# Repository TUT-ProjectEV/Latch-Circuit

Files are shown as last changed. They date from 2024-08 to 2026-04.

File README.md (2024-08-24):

# Latch-Circuit

## Version
- v1.1

## Overview
- AMS, BSPD, IMDからの信号をモニタ・ラッチしてSDN回路に接続されるリレーをドライブする回路
- AMS, BSPD, IMDのインジケータドライブ回路

## Requirement
### Development
- Kicad 7.0
### Libraries
- ProjectEV-Kicad-Library
    - v7.0

## Usage
- Vsupply: 12V
- AMS, BSPD, IMD Signal Input Level: L=0V, H=12V

## Features
- MOSFETによるラッチング、リレードライブ
- AMS, BSPD, IMD信号入力はMOSFETのゲートであるため、ロジックレベルは3.3V~12Vまで対応可能

## Reference
- ["Reference Site Name"]("Reference URL")

## Author
- [ST04-tkmr](https://github.com/ST04-tkmr)

## License
- Copyright (c) 2024 東京工科大学 ProjectEV

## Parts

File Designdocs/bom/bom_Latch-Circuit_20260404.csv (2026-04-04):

Reference | Value | Footprint | Qty | DNP | Mouser番号 | digikey品番
C1 | 22u | ProjectEV_Capacitor:C_3216M | 1
C2,C4,C5,C6 | 10n | ProjectEV_Capacitor:C_1608M | 4
C3 | 100n | ProjectEV_Capacitor:C_1608M | 1
C7 | 1n | ProjectEV_Capacitor:C_3216M | 1
D1 | PZ1AH11B-AU_R1_000A1 | ProjectEV_Diode:PZ1AH11B-AU_R1_000A1 | 1 |  | 241-PZ1AH11BAUR1000A
D2,D4,D5,D6 | B1911PG--20D000514U1930 | ProjectEV_LED:B1911PG--20D000514U1930 | 4 |  |  | 3147-B1911PG--20D000514U1930CT-ND
D3 | CUHZ20V,H3F | ProjectEV_Protection:CUHZ20V,H3F | 1 |  |  | 264-CUHZ20VH3FCT-ND
D7,D8,D9 | B1911USD-20D000114U1930 | ProjectEV_LED:B1911USD-20D000114U1930 | 3 |  |  | 3147-B1911USD-20D000114U1930CT-ND
F1 | 0ABB-1000-TM | ProjectEV_Fuse:0ABB-1000-TM | 1 |  | 530-0ABB-1000-TM | 507-0ABB-5000-TMCT-ND
J1 | 2-1445052-2 | ProjectEV_Connector:2-1445052-2 | 1 |  | 571-2-1445052-2
J2 | 3-794633-8 | ProjectEV_Connector:3-794633-8 | 1 |  | 571-3-794633-8
J3 | B2P-VH | ProjectEV_Connector_JST:B2P-VH | 1 |  |  | 455-1639-ND
J4 | 3-794633-6 | ProjectEV_Connector:3-794633-6 | 1 |  | 571-3-794633-6
Q1 | DMP3098LQ-7 | ProjectEV_Transistor:DMP3098LQ-7 | 1 |  | 621-DMP3098LQ-7
Q2,Q3,Q4 | 2N7002K-AU_R1_000A2 | ProjectEV_Transistor:2N7002K-AU_R1_000A2 | 3 |  |  | 3757-2N7002K-AU_R1_000A2CT-ND
R1,R2,R8,R9,R12,R15,R28,R29,R30,R31,R32,R33 | 10k | ProjectEV_Resistor:R_1608M | 12
R3,R4,R5,R6 | 0 | ProjectEV_Resistor:R_1608M | 4
R7,R10,R13,R16,R19,R22,R25 | 100 | ProjectEV_Resistor:R_1608M | 7
R11,R14,R17,R20,R23,R26 | 100k | ProjectEV_Resistor:R_1608M | 6
R18,R21,R24 | 1.2k | ProjectEV_Resistor:R_3216M | 3
R27 | 1M | ProjectEV_Resistor:R_3216M | 1
U1,U2,U3 | TLP3106A(TP,F | ProjectEV_Relay:TLP3106A(TP,F | 3 |  | 757-TLP3106A(TP,F
U4 | CD4043BPWR | ProjectEV_Logic:CD4043BPWR | 1 |  | 595-CD4043BPWR
U5 | TBD62003AFNG,EL | ProjectEV_PowerManagement:TBD62003AFNG,EL | 1 |  | 757-TBD62003AFNGEL

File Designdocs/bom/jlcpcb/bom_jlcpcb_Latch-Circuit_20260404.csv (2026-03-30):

Comment | Designator | Footprint | LCSC | Quantity
0 | R3,R4,R5,R6 | R_1608M | C21189 | 4
1.2k | R18,R21,R24 | R_3216M | C22765 | 3
100 | R10,R13,R16,R19,R22,R25,R7 | R_1608M | C22775 | 7
100k | R11,R14,R17,R20,R23,R26 | R_1608M | C25803 | 6
100n | C3 | C_1608M | C14663 | 1
10k | R1,R12,R15,R2,R28,R29,R30,R31,R32,R33,R8,R9 | R_1608M | C25804 | 12
10n | C2,C4,C5,C6 | C_1608M | C57112 | 4
22u | C1 | C_3216M | C12891 | 1
MouseBites_5.0mm_OneSide | REF** | MouseBites_5.0mm_OneSide |  | 1

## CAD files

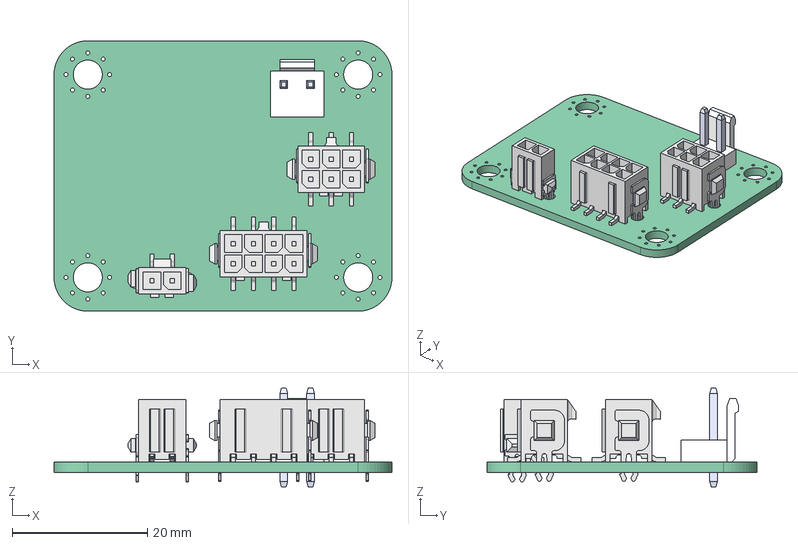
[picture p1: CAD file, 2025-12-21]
Designdocs/3dmodel/Latch-Circuit_20251221.step
50.0 x 40.0 x 14.6 mm

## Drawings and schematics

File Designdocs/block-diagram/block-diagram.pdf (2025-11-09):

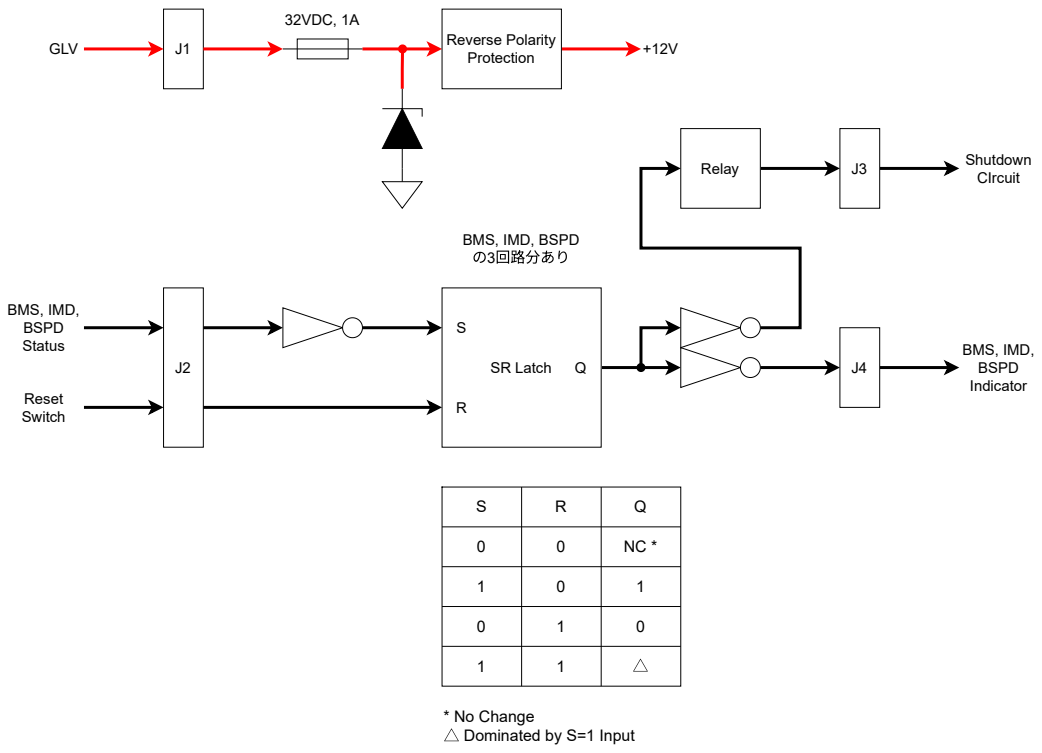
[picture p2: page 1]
32VDC, 1A; Reverse Polarity Protection; GLV; BMS, IMD, BSPD Status; Reset Switch; SR Latch; Relay; Shutdown; CIrcuit; BMS, IMD, BSPD Indicator

BMS, IMD, BSPD
の3回路分あり

* No Change
△ Dominated by S=1 Input

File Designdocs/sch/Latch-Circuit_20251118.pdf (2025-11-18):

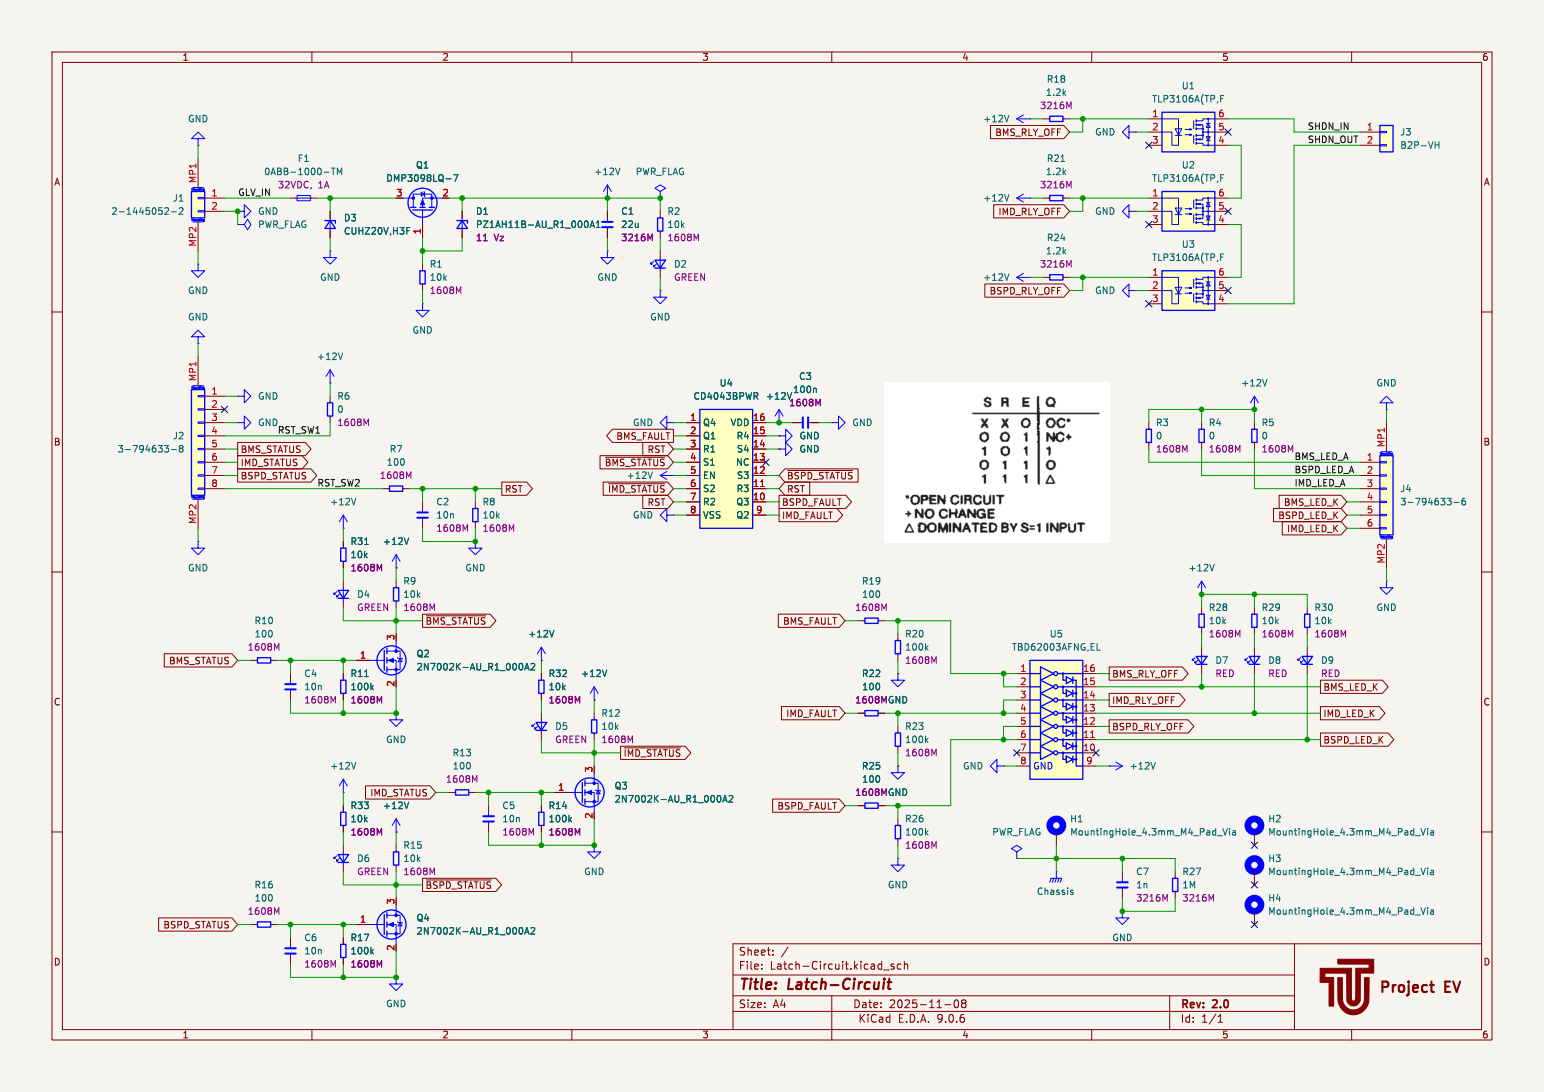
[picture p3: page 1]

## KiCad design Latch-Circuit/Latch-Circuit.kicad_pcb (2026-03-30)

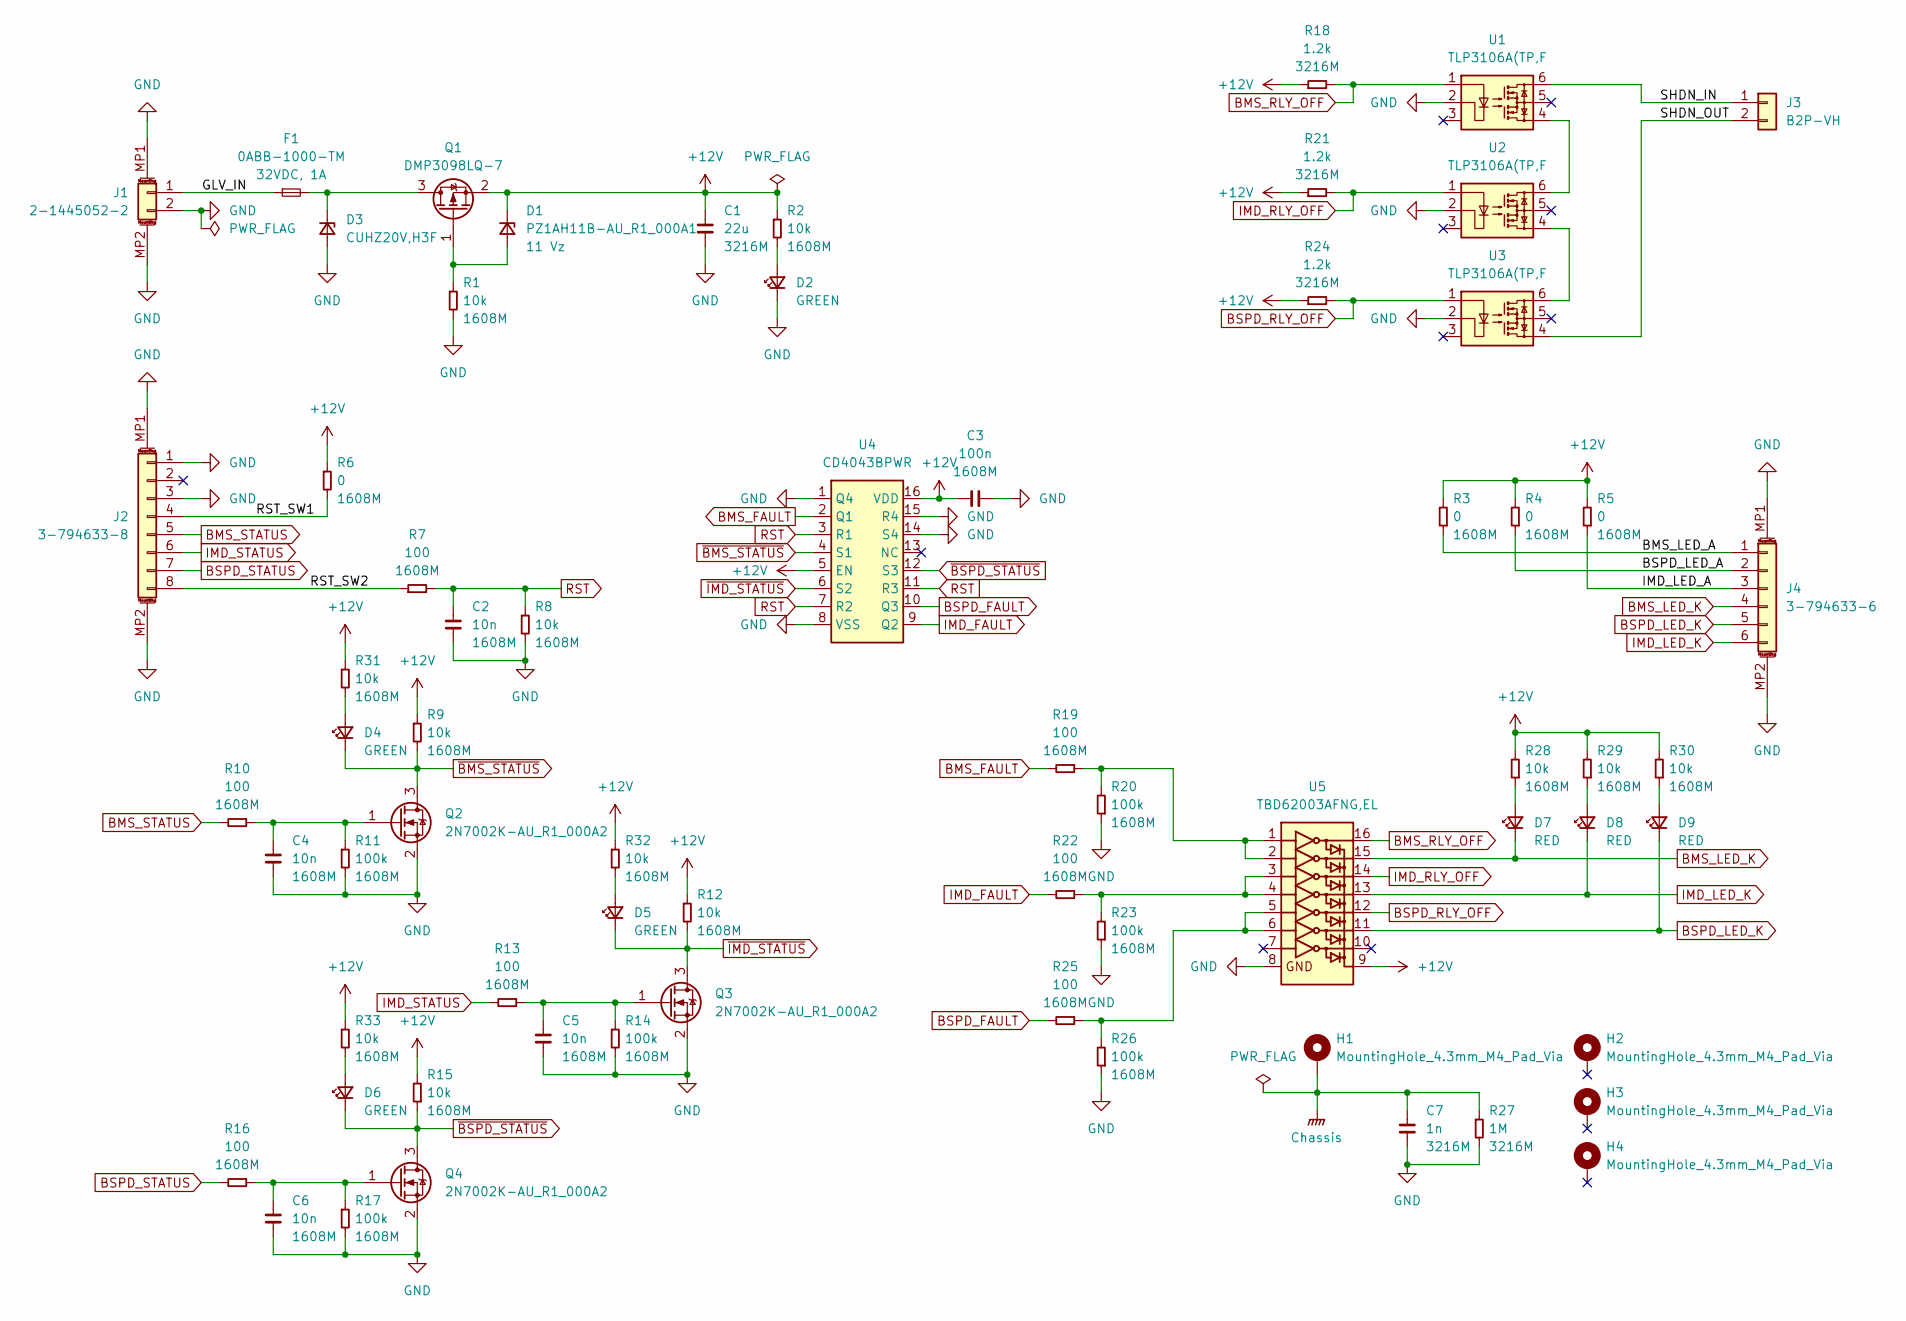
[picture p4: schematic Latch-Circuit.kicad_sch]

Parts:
C1: 22u; C_3216M
C2, C4, C5, C6: 10n; C_1608M
C3: 100n; C_1608M
C7: 1n; C_3216M
D1: PZ1AH11B-AU_R1_000A1; Mouser番号 241-PZ1AH11BAUR1000A
D2, D4, D5, D6: B1911PG--20D000514U1930; digikey品番 3147-B1911PG--20D000514U1930CT-ND
D3: CUHZ20V,H3F; digikey品番 264-CUHZ20VH3FCT-ND
D7, D8, D9: B1911USD-20D000114U1930; digikey品番 3147-B1911USD-20D000114U1930CT-ND
F1: 0ABB-1000-TM; digikey品番 507-0ABB-5000-TMCT-ND
H1, H2, H3, H4: MountingHole_4.3mm_M4_Pad_Via
J1: 2-1445052-2; Mouser番号 571-2-1445052-2
J2: 3-794633-8; Mouser番号 571-3-794633-8
J3: B2P-VH; digikey品番 455-1639-ND
J4: 3-794633-6; Mouser番号 571-3-794633-6
Q1: DMP3098LQ-7; Mouser番号 621-DMP3098LQ-7
Q2, Q3, Q4: 2N7002K-AU_R1_000A2; digikey品番 3757-2N7002K-AU_R1_000A2CT-ND
R1, R2, R8, R9, R12, R15, R28, R29, R30, R31, R32, R33: 10k; R_1608M
R3, R4, R5, R6: 0; R_1608M
R7, R10, R13, R16, R19, R22, R25: 100; R_1608M
R11, R14, R17, R20, R23, R26: 100k; R_1608M
R18, R21, R24: 1.2k; R_3216M
R27: 1M; R_3216M
U1, U2, U3: TLP3106A(TP,F; Mouser番号 757-TLP3106A(TP,F
U4: CD4043BPWR; Mouser番号 595-CD4043BPWR
U5: TBD62003AFNG,EL; Mouser番号 757-TBD62003AFNGEL

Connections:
+12V: C1.1, C3.1, D1.1 (K), Q1.2 (S), R2.1, R3.2, R4.2, R5.2, R6.1, R9.1, R12.1, R15.2, R18.1, R21.1, R24.1, R28.2, R29.2, R30.2, R31.1, R32.1, R33.1, U4.5 (EN), U4.16 (VDD), U5.9 (COMMON)
/BMS_LED_A: J4.1, R3.1
/BSPD_LED_A: J4.2, R4.1
/GLV_IN: F1.1, J1.1
/IMD_LED_A: J4.3, R5.1
/RST_SW1: J2.4, R6.2
/RST_SW2: J2.8, R7.1
/SHDN_IN: J3.1, U1.6 (Drain)
/SHDN_OUT: J3.2, U3.4 (Drain)
BMS_FAULT: R19.2, U4.2 (Q1)
BMS_LED_K: D7.1 (K), J4.4, U5.15 (O2)
BMS_RLY_OFF: R18.2, U1.1 (Anode), U5.16 (O1)
BMS_STATUS: J2.5, R10.2
BSPD_FAULT: R25.2, U4.10 (Q3)
BSPD_LED_K: D9.1 (K), J4.5, U5.11 (O6)
BSPD_RLY_OFF: R24.2, U3.1 (Anode), U5.12 (O5)
BSPD_STATUS: J2.7, R16.2
Chassis: C7.1, H1.MP, R27.1
GND: C1.2, C2.2, C3.2, C4.2, C5.2, C6.2, C7.2, D2.1 (K), D3.2 (A), J1.2, J1.MP1 (MountPin), J1.MP2 (MountPin), J2.1, J2.3, J2.MP1 (MountPin), J2.MP2 (MountPin), J4.MP1 (MountPin), J4.MP2 (MountPin), Q2.2 (S), Q3.2 (S), Q4.2 (S), R1.2, R8.2, R11.2, R14.2, R17.2, R20.1, R23.1, R26.1, R27.2, U1.2 (Cathode), U2.2 (Cathode), U3.2 (Cathode), U4.1 (Q4), U4.8 (VSS), U4.14 (S4), U4.15 (R4), U5.8 (GND)
IMD_FAULT: R22.2, U4.9 (Q2)
IMD_LED_K: D8.1 (K), J4.6, U5.13 (O4)
IMD_RLY_OFF: R21.2, U2.1 (Anode), U5.14 (O3)
IMD_STATUS: J2.6, R13.2
unnamed: D1.2 (A), Q1.1 (G), R1.1
unnamed: D2.2 (A), R2.2
unnamed: D3.1 (K), F1.2, Q1.3 (D)
unnamed: D4.2 (A), R31.2
unnamed: D5.2 (A), R32.2
unnamed: D6.2 (A), R33.2
unnamed: D7.2 (A), R28.1
unnamed: D8.2 (A), R29.1
unnamed: D9.2 (A), R30.1
unnamed: C4.1, Q2.1 (G), R10.1, R11.1
unnamed: C5.1, Q3.1 (G), R13.1, R14.1
unnamed: C6.1, Q4.1 (G), R16.1, R17.1
unnamed: U1.4 (Drain), U2.6 (Drain)
unnamed: U2.4 (Drain), U3.6 (Drain)
unnamed: R19.1, R20.2, U5.1 (I1), U5.2 (I2)
unnamed: R22.1, R23.2, U5.3 (I3), U5.4 (I4)
unnamed: R25.1, R26.2, U5.5 (I5), U5.6 (I6)
RST: C2.1, R7.2, R8.1, U4.3 (R1), U4.7 (R2), U4.11 (R3)
~BMS_STATUS: D4.1 (K), Q2.3 (D), R9.2, U4.4 (S1)
~BSPD_STATUS: D6.1 (K), Q4.3 (D), R15.1, U4.12 (S3)
~IMD_STATUS: D5.1 (K), Q3.3 (D), R12.2, U4.6 (S2)

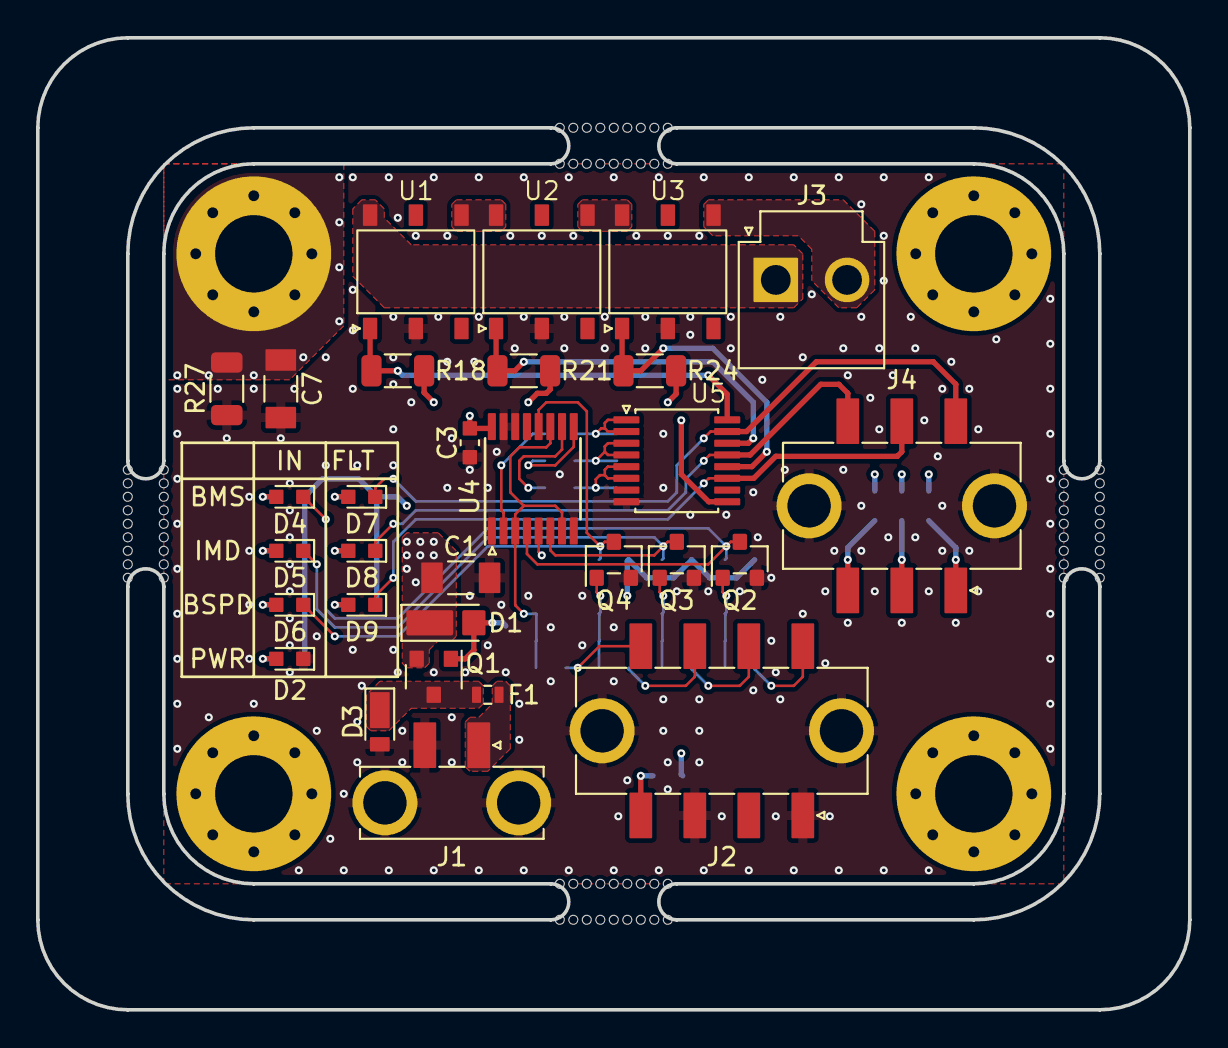
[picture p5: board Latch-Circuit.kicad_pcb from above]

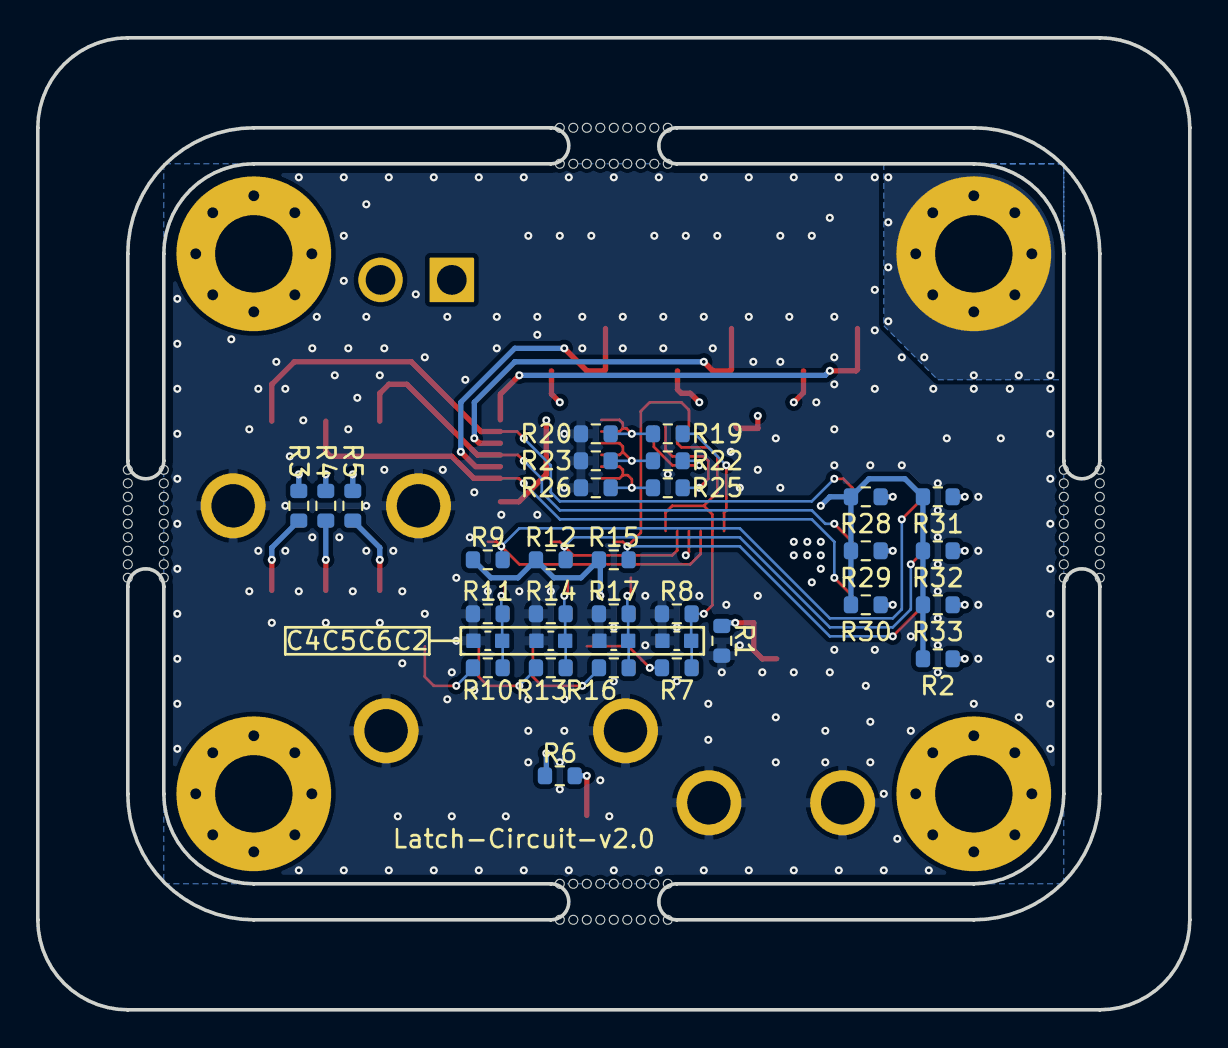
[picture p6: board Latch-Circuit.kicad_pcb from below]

Board: 4 copper layers, 64.0 x 54.0 mm, 67 parts (33 on the bottom side), 44 nets.

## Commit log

2024-03-17 create project
    [Latch-Circuit.kicad_pcb, Latch-Circuit.kicad_sch]
2024-03-17 add ignore folder
    Latch-Circuit-backups
2024-04-20 add sim file
    シミュレーション済み
2024-04-20 回路図完成、PCBCADに部品追加
    [Latch-Circuit.kicad_pcb, Latch-Circuit.kicad_sch]
2024-04-22 ラベル追加
    [Latch-Circuit.kicad_sch]
2024-04-22 若干配置
    [Latch-Circuit.kicad_pcb]
2024-04-24 コネクタをトップ型に変更、アノテーション、素子配置
    [Latch-Circuit.kicad_pcb, Latch-Circuit.kicad_sch]
2024-04-24 配線完了、リレー配線修正、外周ビア打ち
    [Latch-Circuit.kicad_pcb, Latch-Circuit.kicad_sch]
2024-04-25 完成
    最終チェック後、ガーバー出力
    [Latch-Circuit.kicad_pcb]
2024-04-25 原点位置の修正
    [Latch-Circuit.kicad_pcb]
2024-04-26 シャットダウンチェック用のTP追加
    [Latch-Circuit.kicad_pcb, Latch-Circuit.kicad_sch]
2024-04-28 1ピン識別子追加
    [Latch-Circuit.kicad_pcb]
2024-04-29 コメント追加
    [Latch-Circuit.kicad_sch]
2024-05-03 ベタ修正
    [Latch-Circuit.kicad_pcb]
2024-05-03 ガーバー、BOM出力
    [bom.csv, designators.csv, positions.csv]
2024-05-20 digikey用bom作成
    購入数未入力、他基板素子と同時発注のため
    [bom.xlsx, digikey-list.xlsx]
2024-05-20 ファイル名変更
    [bom_Latch-Circuit.xlsx, digikey-list_Latch-Circuit.xlsx]
2024-05-23 素子の説明追加
    [digikey-list_Latch-Circuit.xlsx]
2024-05-23 購入個数追加、csv出力
    [digikey-list_Latch-Circuit.csv, digikey-list_Latch-Circuit.xlsx]
2024-07-29 modify constant, add NOT for status LED
2024-07-29 modify constant, add circuits Rgs 1M->100k, NOT Circuit for status LED, LED for test
    [Latch-Circuit.kicad_sch]
2024-07-29 配置、配線終了
    [Latch-Circuit.kicad_pcb]
2024-07-30 complete AW, DRC next->select parts at JLCPCB
    [Latch-Circuit.kicad_pcb]
2024-07-30 PCBA用素子選定
2024-07-30 export step
    [Latch-Circuit.step]
2024-07-30 add 捨て基板, Toolinghole, Fiducial
    [Latch-Circuit.kicad_pcb]
2024-07-30 generate gerber, production file by JLCPCB Tools
    [BOM-Latch-Circuit.csv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]
2024-07-30 原点修正
    [Latch-Circuit.kicad_pcb]
2024-07-30 generate gerber and production files again
    [CPL-Latch-Circuit.csv, Latch-Circuit-CuBottom.gbr, Latch-Circuit-CuTop.gbr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]
2024-08-05 add JLCPCB PCBA BOM
    [bom.xls]
2024-08-23 README.md を更新
2025-11-08 create a new kicad project
    [Latch-Circuit.kicad_pcb, Latch-Circuit.kicad_sch]
2025-11-08 add title, revision, and date
    [Latch-Circuit.kicad_sch]
2025-11-08 add signal labels and power circuit
    [Latch-Circuit.kicad_sch]
2025-11-08 complete circuit design, not decide constraints
    [Latch-Circuit.kicad_sch]
2025-11-09 modify pin assigns, decide consts, and apply some changes
    [Latch-Circuit.kicad_sch]
2025-11-09 ERC done, and modify
    [Latch-Circuit.kicad_sch]
2025-11-09 create a new drawio project and add power circuit
2025-11-09 add footprints from sch
    [Latch-Circuit.kicad_pcb]
2025-11-09 add LEDs
    [Latch-Circuit.kicad_sch]
2025-11-09 change relay and led drive circuit
    [Latch-Circuit.kicad_sch]
2025-11-09 update relay and led drive circuit
2025-11-09 update footprints, and place components
    [Latch-Circuit.kicad_pcb]
2025-11-09 finish wiring
    [Latch-Circuit.kicad_pcb]
2025-11-15 add vias
    [Latch-Circuit.kicad_pcb]
2025-11-18 generate pdf of sch
    [Latch-Circuit.kicad_sch]
2025-11-18 add dimension line and DRC OK
    [Latch-Circuit.kicad_pcb]
2025-11-18 add jlcpcb tools database
    [Latch-Circuit.kicad_pcb]
2025-12-21 add pcb name
    [Latch-Circuit.kicad_pcb]
2026-03-30 add breakaway panels and mousebites
    [Latch-Circuit.kicad_pcb]
2026-03-30 generate production files
    [BOM-Latch-Circuit.csv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]
2026-03-30 toggle BOM
    [BOM-Latch-Circuit.csv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]
2026-04-04 update bom
    [BOM-Latch-Circuit.csv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]
2026-04-04 move a file
    [Latch-Circuit_20251221.step]
2026-04-04 generate bom
    [Latch-Circuit.kicad_sch, bom_Latch-Circuit_20260404.csv]
2026-04-04 add gerber
2026-04-04 add BOM and CPL for JLCPCB
    [bom_jlcpcb_Latch-Circuit_20260404.csv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]
